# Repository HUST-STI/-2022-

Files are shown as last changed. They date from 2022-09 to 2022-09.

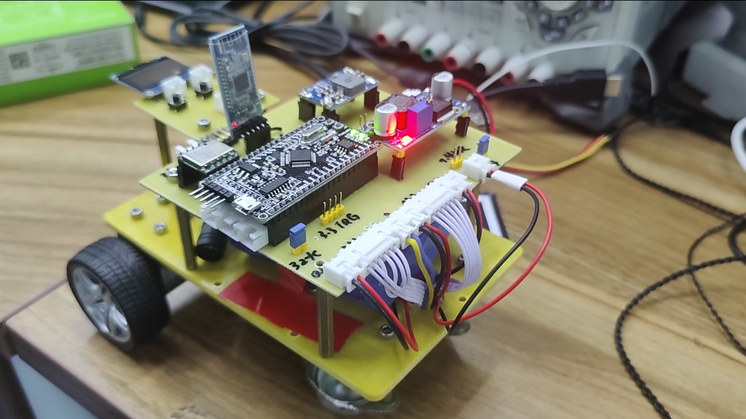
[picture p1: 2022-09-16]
小车图片.png

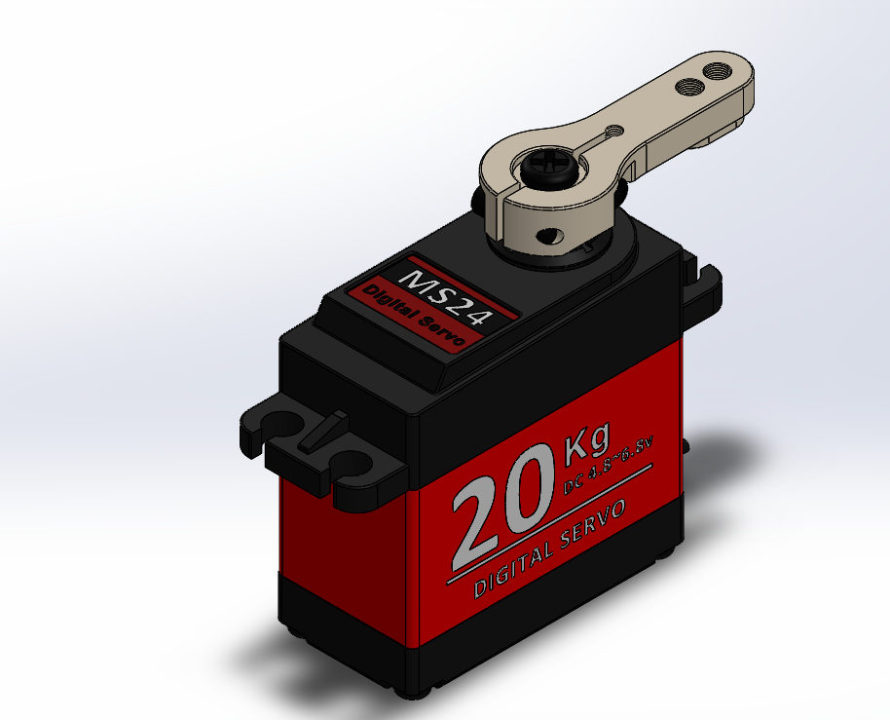
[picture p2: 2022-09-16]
机械结构/云台支架/000483伺服舵机外形模型3D图/三维总图.png

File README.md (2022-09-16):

# -2022暑期培训模拟题激光引导小车-
## 程序说明

由于是模拟题，所以就不详细介绍了，具体说说各部分怎么实现的就行

1. 小车云台通讯：两个BT-05蓝牙模块
2. 确保小车走直线：使用JY-901陀螺仪进行角度闭环，注意要设置该陀螺仪为六轴算法，这样角度才能用，九轴会飘
3. 确保小车走到指定格子：电机编码器速度环加位置环
4. 寻路算法：详见报告
5. 激光笔指到指定格子：定死云台位置，直接开环标定
6. 识别数字：Jetson Nano跑神经网络
7. 遥控选择数字：使用Arduino Uno连接红外接收头，收到信号后给STM32发信息即可。这样做是因为Arduino有现成的红外库，使用方便

## 机械说明

小车用的是牛眼轮差速转向结构，这种结构适合在小范围内灵活移动，为了确保不打滑，小车重心应该压在后轮上。

云台没什么好说的，就是直接用2020铝材支起来一个架子，在架子上放电路。舵机固定方式看文件内的Solidwork文件。

工程来自K06

2022.9.16

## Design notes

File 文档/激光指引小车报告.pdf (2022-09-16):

## 激光引导小车

摘要：本系统实现了一个激光发射云台和一辆激光引导的小车。云台利用 STM32 主控制

器完成舵机控制，驱动激光笔的运动，采用 Jetson Nano 作为图像处理单元，通过深度神经

网络完成数字和黑块的识别功能，选用BT-05蓝牙模块作为通信单元。小车系统利用STM32

主控制器和电机驱动模块完成电机控制，驱动小车运动，通过 BT-05 蓝牙模块与云台进行

通信。最终，云台可以实现识别数字和障碍块、使激光指向目标点、与小车通信等功能；

小车可以完成接收云台信号，移动到指定目标点并返回等任务。

关键词：神经网络；运动控制；PID 算法。

第1页

一、 系统方案

1. 比较与选择

1.1 机器视觉方案

方案一：OpenMV

方案二：Jetson Nano

方案比较与选择： 方案一使用 OpenMV 进行视觉处理。使用该模块进行图像处理十分简

单便捷，且不会存在自启动、开发环境配置等问题。但受处理器性能限制，OpenMV 的处

理速度慢、运行内存小，不适合复杂的图像处理。方案二采用 Jetson Nano 上运行 OpenCV

的方式进行图像处理。该方案优点是 Jetson Nano 搭载了 NVIDIA 显卡，处理速度块，运行

内存大，而且 OpenCV 内置函数功能齐全，完全满足复杂的图像处理需求。但缺点是与

STM32 通讯困难且开发流程繁琐。在本装置中，为增强系统对数字识别的准确度，需要使

用深度神经网络来提取图片特征并推理，运算复杂而且涉及到多帧图像处理，速度慢、内

存小的 OpenMV 已不能满足系统的需求。因此选择 Jetson Nano 进行图像识别。

1.2 小车底盘方案选择

方案一：阿克曼转向

方案二：后轮差速转向

方案比较与选择：方案一的优点在于控制算法比较简单，只需要控制前轮转角即可控制小

车的转向角度；缺点是小车的体积会比较大，小车转弯半径大，不适合大角度转弯、掉头

等操作。方案二的优点在于小车可以进行原地掉头等灵活的运动，小车体积小；缺点是小

车只能在比较平坦的地面上行进。在激光引导小车任务中，地形平坦，需要小车进行灵活

的运动。综合分析，选择两轮差速转向结构。

1.3 直行矫正方案选择

方案一：阿克曼转向

方案二：后轮差速转向

方案比较与选择：方案一的优点在于摄像头可以实时反映小车前进方向偏离路径中心线的

距离，实现小车绝对地直行；缺点在于算法复杂，并且需要额外的处理器和外围电路。方

案二的优点在于角度传感器的电路和算法并不复杂，模块体积小，功耗低，使用起来十分

方便；缺点为角度传感器的零点方向并不一定与行驶方向重合，有一定的偏差。在激光引

导小车任务中，小车的行驶路线并不复杂，任务对小车的行驶角度要求不高，综合分析，

选择角度传感器矫正方案。

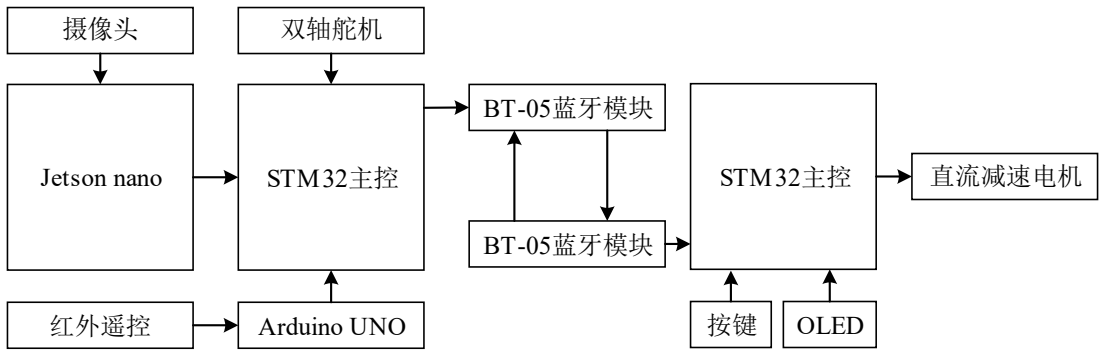
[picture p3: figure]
STM32主控; 直流 速电机; BT-05蓝牙模块; Jetson nano; 摄像头; 红外遥控; Arduino UNO

第2页

2. 方案描述

系统框图如图 1 所示。本系统通过 Arduino 主控的红外遥控系统控制激光笔指向区域和

小车运动的模式。系统使用 Jetson Nano 作为图像处理单元，通过图像处理的方式获得地图障

碍区域位置，并通过 UART 串口通讯将数据传输给 STM32 主控制器。主控制器接收到数据

后控制云台舵机姿态和小车的直流编码电机，将激光笔指向指定区域并控制小车避开障碍到

达目的区域。云台和小车之间通过 BT-05 蓝牙模块实现通讯。

图 1 系统框图

二、 理论分析与计算

1. 数字识别

数字识别部分采用深度神经网络模型 Yolov4-tiny。其结构图如图 2 所示。Yolov4-tiny

模型的参数量只有 600 万，在目标检测领域的深度神经网络中参数量较少，比较适合在嵌

入式设备上进行实时检测推理。其整体网络结构共有 38 层，使用了三个残差单元，激活函

数使用了 LeakyReLU,目标的分类与回归使用两个特征层，合并有效特征层时使用了特征

金字塔网络。其同样使用了 CSPnet 结构，并对特征提取网络进行通道分割，将经过 3x3 卷

积后输出的特征层通道划分为两部分，并取第二部分。相较于其它深度识别网络，Yolov4-

tiny 的实时性和准确率均有所提高。

在本装置中，使用现场拍摄的的照片作为原始数据集，一种拍摄了约 900 张图片，包

含 8 中数字。对原始数据集做 Mosaic 数据增强后得到月 4000 张数据集。将其划分为训练

集和测试集后送入模型中训练。最终得到的测试集精度达到了 90%以上，经实际测试，模

型的泛化误差较小，检测帧率能够达到 20 帧左右，符合设定的任务要求。

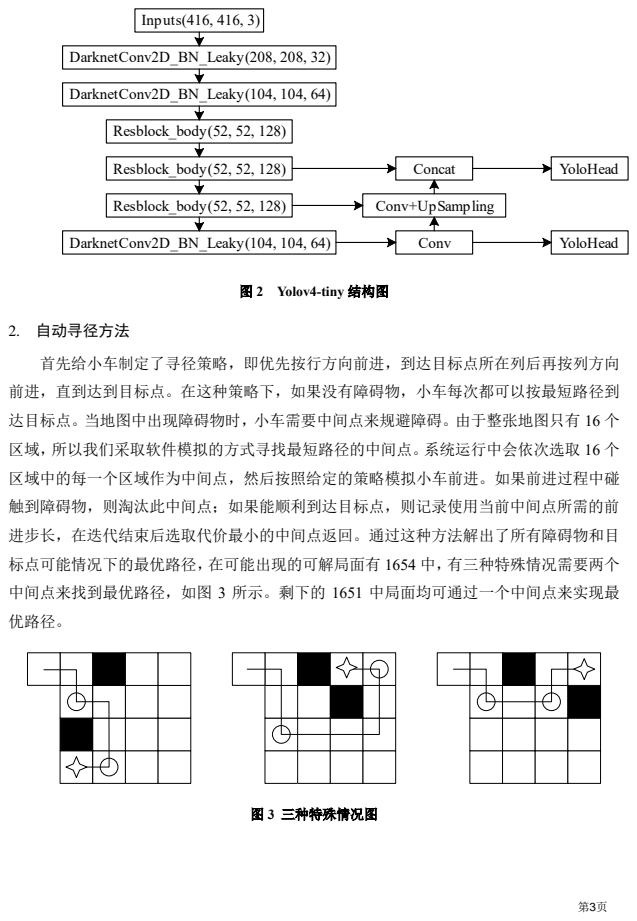
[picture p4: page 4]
图 2 Yolov4-tiny 结构图; 2. 自动寻径方法; 图 3 三种特殊情况图; Inputs 416, 416, 3; DarknetConv2D BN Leaky 208, 208, 32; DarknetConv2D BN Leaky 104, 104, 64; Concat; Yolo ead; Conv

Res lock ody 52, 52, 128

Conv UpSa plin

首先给小车制定了寻径策略，即优先 行方向前进，到达目标点所在列后再 列方向
前进，直到达到目标点。在这种策略下，如果没有障碍物，小车每次都可以 最短路径到
达目标点。当地图中出现障碍物时，小车需要中间点来规避障碍。由于整张地图只有 16 个
区域，所以我们采取软件模拟的方式寻找最短路径的中间点。系统运行中会依次选取 16 个
区域中的每一个区域作为中间点，然后 照给定的策略模拟小车前进。如果前进过程中碰
触到障碍物，则淘汰此中间点；如果能顺利到达目标点，则记录使用当前中间点所需的前
进步长，在迭代结束后选取代价最小的中间点返回。通过这种方法解出了所有障碍物和目
标点可能情况下的最优路径，在可能出现的可解局面有 1654 中，有三种特殊情况需要两个
中间点来找到最优路径，如图 3 所示。剩下的 1651 中局面均可通过一个中间点来实现最
优路径。

第4页

3. 两轮差速底盘结构

本小车的底盘采用两轮差速底盘结构，该结构通过两个橡胶车轮和两个牛眼轮对底盘

进行支撑，如图 4 所示。

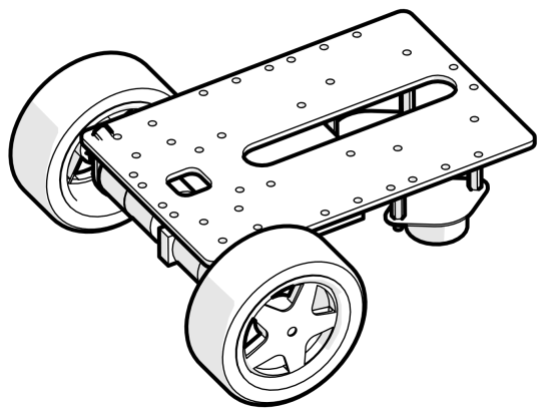
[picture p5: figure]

图 4 两轮差速底盘结构
设车体速度为 v，左轮速度为
l

v

，右轮速度为
r

v

，车体自转速度为
ω

，转弯半径为 R，

两轮之间距离为 D，两轮到车中心的距离为 d，右轮到圆心距离为 L。我们可以推算出整

车角速度和两轮速度之间的关系如下

角速度、速度和运动半径之间的物理关系：

| | v | R =ω*
3.1
左轮、右轮速度分解：
*( | ) | *( | 2 ) | *( | ) l
v | L D | L | d | R d | d = | + | = | + | = | + | = ω | ω | ω | ω
3.2
* | *( | ) r | l v | v | L | R d | v | d = | = | = | − | = − ω | ω | ω
3.3
和速度等于两轮速度之和的一半：
* | *( | )
2
l | r v | v v | R | L d ω | ω
+
= | = | + | =

3.4

角速度和两轮差速之间的关系如式 3.5 所示：

2

l | r v | v
d

ω

−
=

3.5

因此只要控制两个车轮的差速，小车就可以进行前进、后退、转向和原地掉头等操作。

4. 串级 PID 与直行矫正

我们采用 PID 算法对小车每个车轮的转动速度和转动角度进行控制。在小车从初始区

域出发到达指定区域过程中，只使用了速度环来控制小车的前行速度。

电机在转动时，单片机会对编码器输出的矩形波进行捕获，随后计算出电机的实时转

速反馈到输出到电机的 PWM 信号中，实现对速度的控制。

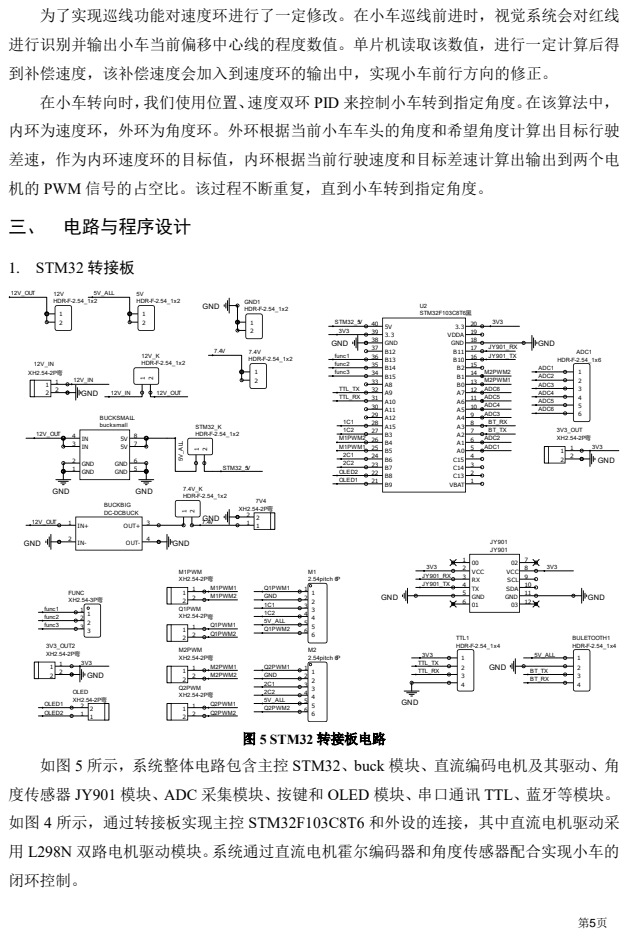
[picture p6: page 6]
三、 电路与程序设计; 1. STM32 转接板; 图 5 STM32 转接板电路; 路电机驱动模块。系统通过直流电机霍尔编码器和角度传感器配合实现小车的

为了实现巡线功能对速度环进行了一定修改。在小车巡线前进时，视觉系统会对红线
进行识别并输出小车当前偏移中心线的程度数值。单片机读取该数值，进行一定计算后得
到补偿速度，该补偿速度会加入到速度环的输出中，实现小车前行方向的修正。
在小车转向时，我们使用位置、速度 环 PID 来控制小车转到指定角度。在该算法中，
内环为速度环，外环为角度环。外环根据当前小车车头的角度和希望角度计算出目标行驶
差速，作为内环速度环的目标值，内环根据当前行驶速度和目标差速计算出输出到两个电
机的 PWM 信号的占空比。该过程不断重复，直到小车转到指定角度。

如图 5 所示，系统整体电路包含主控 STM32、 uck 模块、直流编码电机及其驱动、角
度传感器 JY901 模块、ADC 采集模块、 键和 OL D 模块、串口通讯 TTL、蓝牙等模块。
如图 4 所示，通过转接板实现主控 STM32F103C8T6 和外设的连接，其中直流电机驱动采
闭环控制。

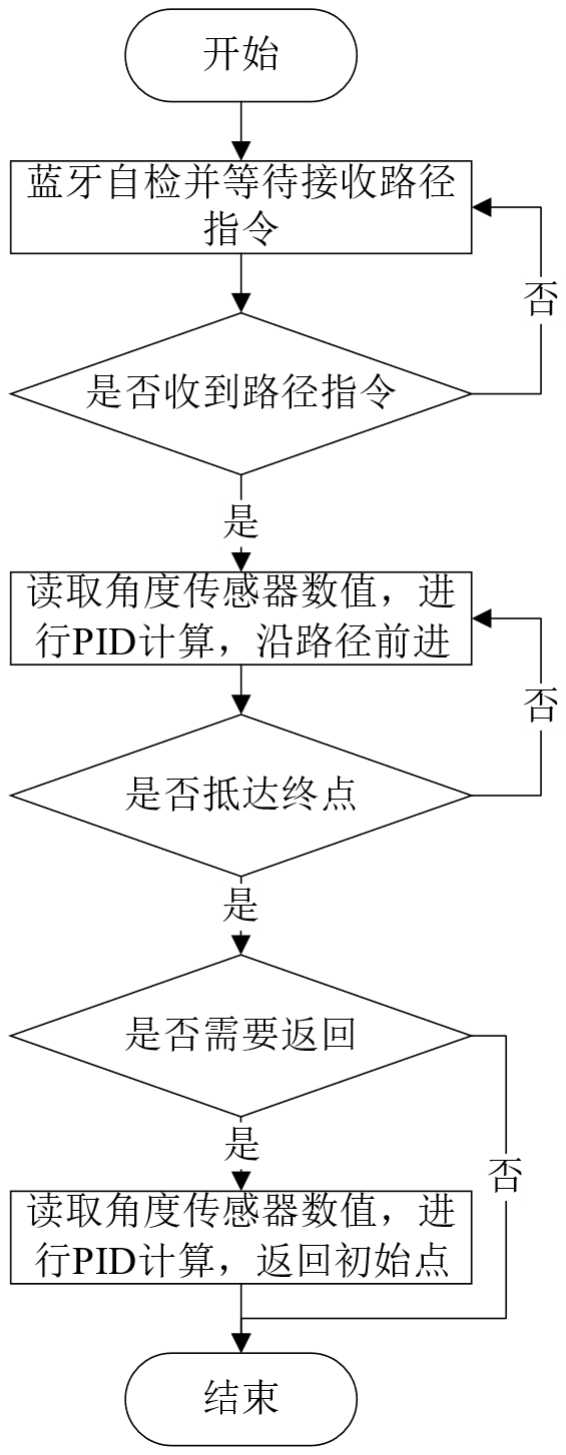
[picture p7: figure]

第6页

2. 软件程序设计

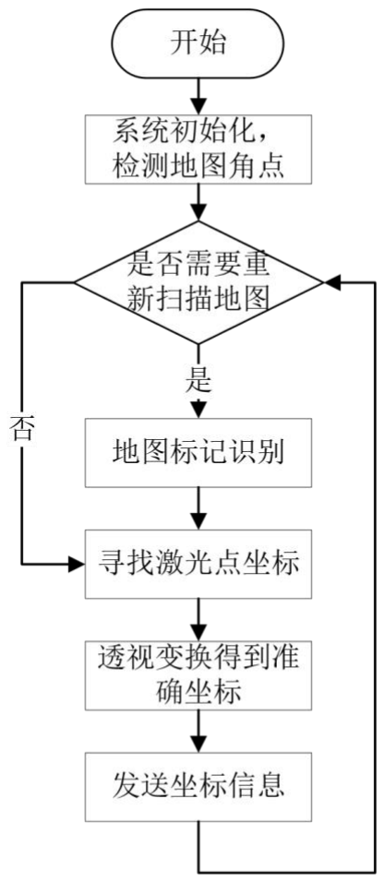
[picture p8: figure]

图 6 程序框图
小车在程序开始后，会先进入蓝牙传输自检阶段，只有收到来自云台的指令，程序才 会进入路径接收阶段。在路径接收阶段中，小车会等待接收云台发送的路径，路径包括 一个中间点和目标点。小车会 照一定的路线先行驶到中间点，随后再行驶到终点。如 果需要返回停车坪，小车会在停止 2 秒后原路返回。

四、 测试方案与测试结果

测试环境

类型 | 品牌 | 型号
电源 | Zhon Ce | DF1743003C 型稳压源
其他 | 卡西欧 | S-70W 型秒表

第7页

1. 测试方案

1.1 基本要求

控制激光笔指向 0、1、4、5 区域，摄像头识别激光点并控制小车移动到指定区域，停

留超过 2s，记录激光笔指向区域编号和总运动时间；在此基础上新增 2、6、8、9、A 区域，

重复上述操作；在此基础上控制激光笔指向任何一个区域，重复上述操作。

1.2 发挥部分

选取场地中的 1 个区域为障碍区域，并使用黑色色块覆盖，控制激光笔指向非障碍区

域，摄像头识别激光点并控制小车绕过障碍区域移动到指定区域，停留超过 2s，记录激光

笔指向区域编号、障碍区域编号和总运动时间；在此基础上选取场地中的 2 个区域为障碍

区域，重复上述操作；在此基础上不重复交换任意两组区域，重复上述操作。

2. 测试结果与数据

2.1 基本要求
表 1 基础部分测试
序号 | 指向区域编号 | 总运动时间/s
1 | 4 | 5.4
2 | 6 | 11.5
3 | B | 15.3
4 | F | 17.9

2.2 发挥部分
表 2 发挥部分：两个小车协同送药测试
序号 | 指向区域编号 | 障碍区域编号 | 总运动时间/s
1 | 6 | 2 | 13.3
2 | A | 6 | 15.9
3 | 7 | 3、6 | 23.3
4 | C | 8、9 | 27.4

第8页

3. 测试结果分析

3.1 基础要求

由测试结果知，系统控制激光笔指向任何区域，摄像头识别激光点并控制小车移动到

指定区域停留超过 2s，均满足题目要求。

3.2 发挥部分

由测试结果知，选取 1 个或者 2 个区域为障碍区域，系统控制激光笔指向非障碍区域，

摄像头识别激光点并控制小车绕过障碍区域移动到指定区域，满足题目要求。在测试过程

途中车身投影未接触障碍区域，很好的完成了题目的要求。

综上所述，本系统能够完成题目的基本要求和发挥要求。

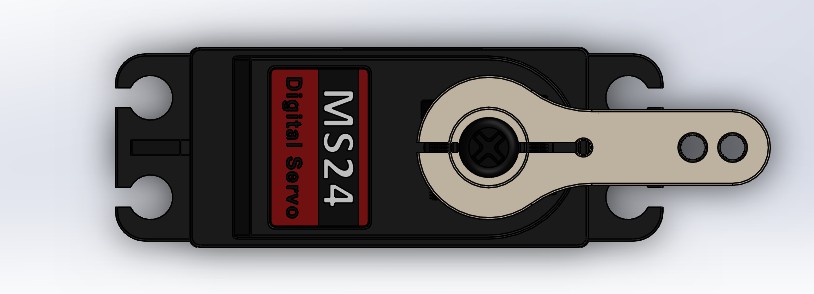
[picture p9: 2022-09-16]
机械结构/云台支架/000483伺服舵机外形模型3D图/俯视图.png

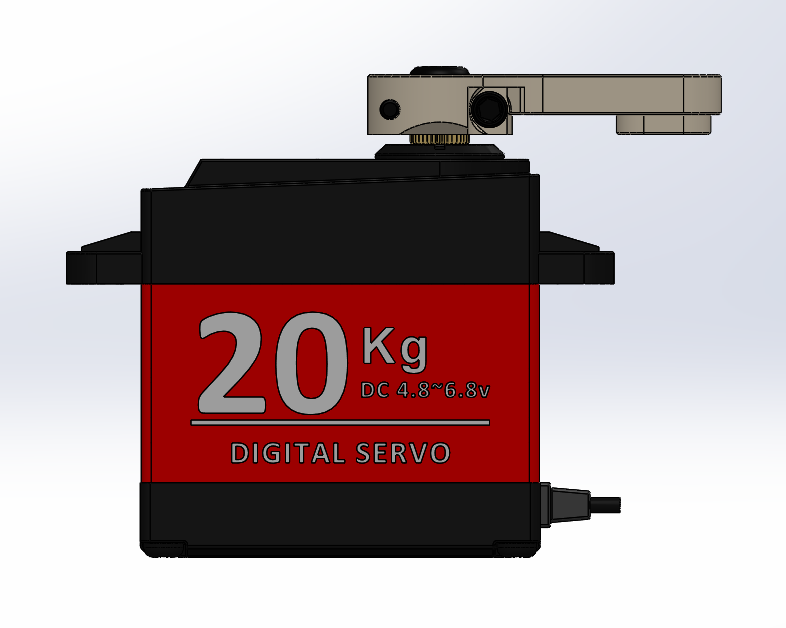
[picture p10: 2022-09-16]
机械结构/云台支架/000483伺服舵机外形模型3D图/主视图.png

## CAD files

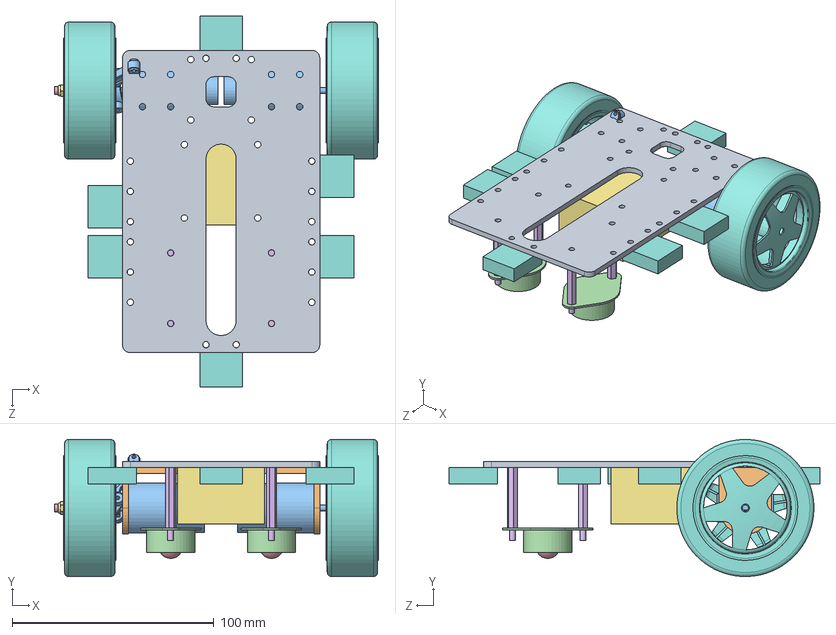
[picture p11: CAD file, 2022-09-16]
机械结构/车/激光引导小车装配体.SLDASM
160.9 x 68.0 x 184.0 mm
车底板
JGA25-370直流减速电机支架 x 2
MG310电机（霍尔编码器） x 2
CY-12A万向球 x 2
CY-12A万向球的球 x 2
铜柱 高20M3螺纹 x 4
L298N简化
l轮子T x 2
灰度传感器 x 6

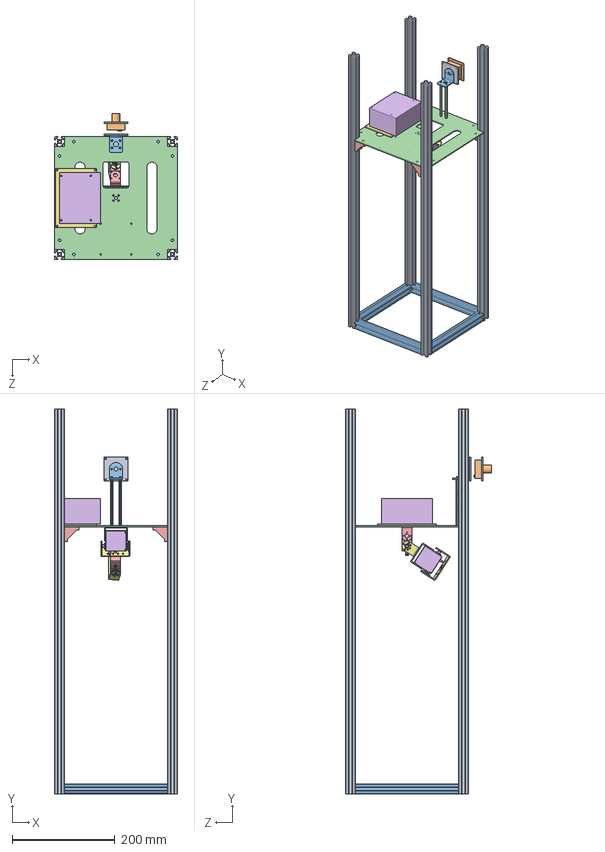
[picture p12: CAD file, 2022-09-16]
机械结构/云台支架/摄像头支架.SLDASM
239.8 x 750.0 x 284.8 mm
竖直支撑钢管 x 4
1车摄像头
摄像头支架横着 x 4
云台支撑板
RDS3115短U支架 x 2
RDS3115 x 2
RDS3115长U支架 x 2
舵机副转盘 x 2
1车摄像头转接2
1车摄像头转接
JGA25-370直流减速电机支架
铜柱 高20M3螺纹 x 6
钢管转角小三角 x 4

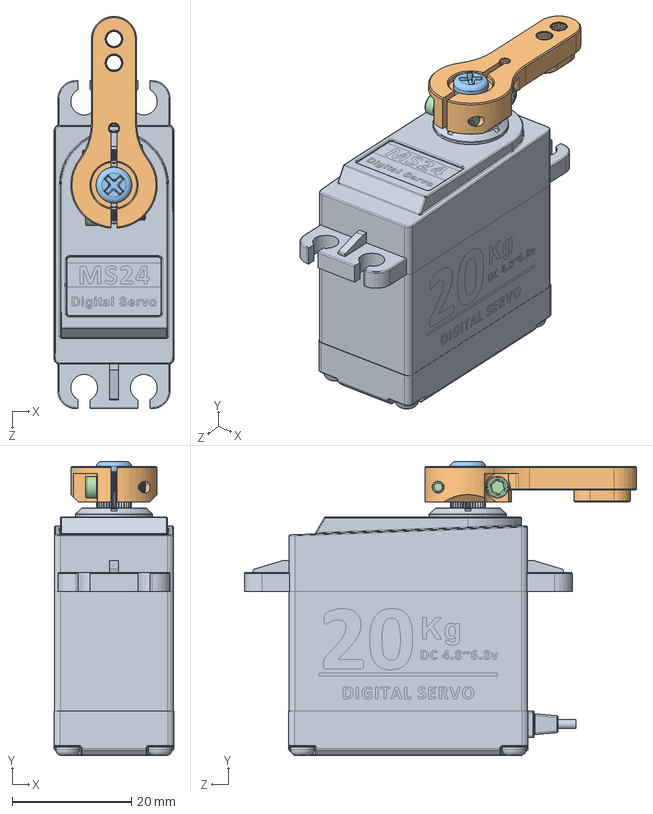
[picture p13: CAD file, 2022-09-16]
机械结构/云台支架/000483伺服舵机外形模型3D图/DIGITAL SERVO ASSEMBLY.SLDASM
20.1 x 49.3 x 65.8 mm
DS3218MG MS24 Digital Servo 270
Servo Arm for DS3218MG
Screw-01 for DS3218MG
Screw-02 for DS3218MG x 2

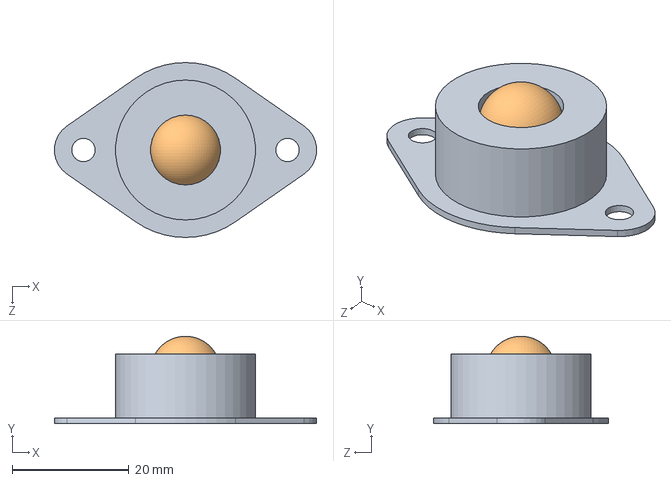
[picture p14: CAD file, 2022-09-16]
机械结构/车/CY-12A万向球组合体.SLDASM
44.9 x 15.0 x 30.0 mm
CY-12A万向球
CY-12A万向球的球

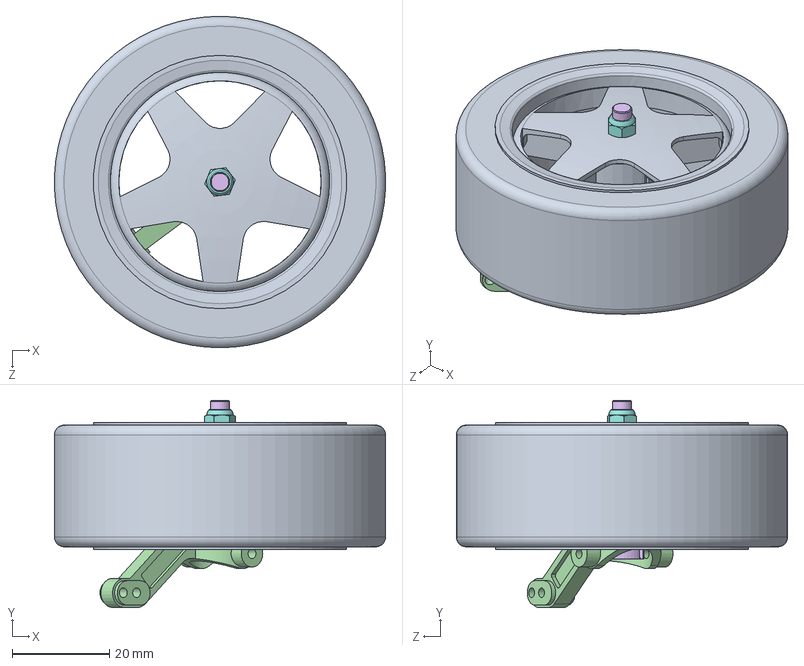
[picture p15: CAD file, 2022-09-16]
机械结构/车/转向结构新/轮子套件.SLDASM
67.9 x 42.5 x 68.0 mm
l轮子T
0388轴承
0288轴承
转向杯
六角轮座
金属轮座轴 新
圆销
GB6170-M4自锁-ZN-10

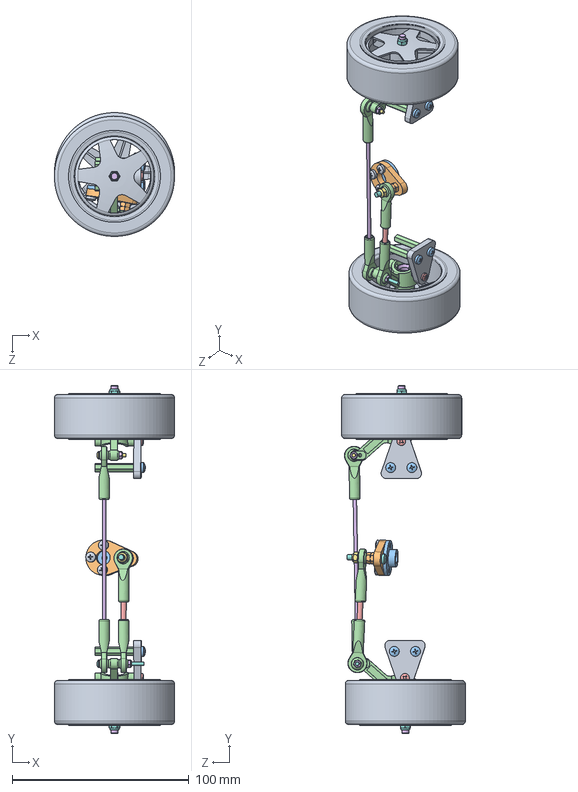
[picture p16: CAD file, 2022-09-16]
机械结构/车/转向结构新/转向套件.SLDASM
68.0 x 196.9 x 70.1 mm
l轮子T x 2
0388轴承 x 2
0288轴承 x 2
转向杯 x 2
六角轮座 x 2
金属轮座轴 新 x 2
圆销 x 2
GB6170-M4自锁-ZN-10 x 2
板1 x 2
板2
金属舵盘
球头轴承 x 4
螺杆m3x25
螺杆m3x75
GB6170-M3（自锁）
GB818-M3X20-ZN-4.8
GB818-M3X6-ZN-4.8 x 3
GB6170-M3-ZN-10 x 2
GB818-M3X8-ZN-4.8 x 4
M3X20双通铜柱 - 副本 x 4
GB845-ST38 x 2
GB6170-M2（自锁） x 2
GB818-M2X15
GB818-M2X25

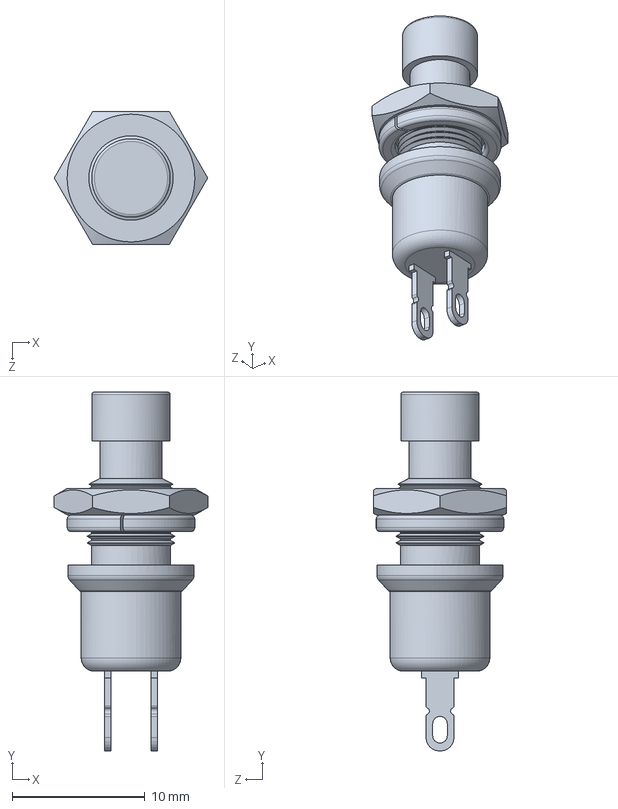
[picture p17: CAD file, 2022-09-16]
机械结构/云台支架/000483伺服舵机外形模型3D图/Momentary Switch Red Cap.SLDPRT
11.5 x 27.0 x 10.0 mm

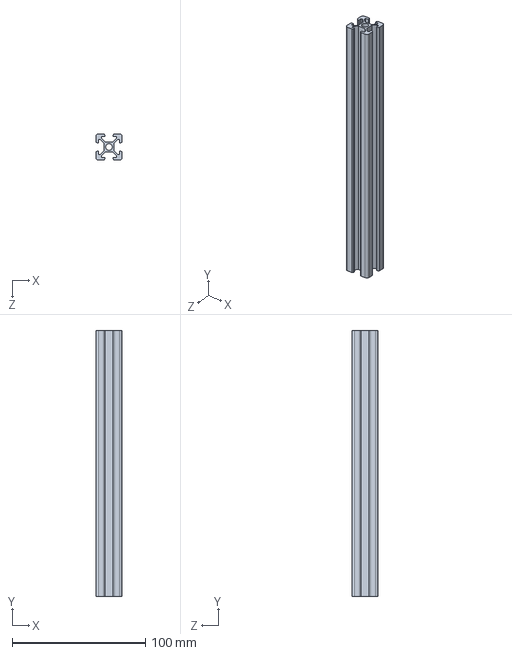
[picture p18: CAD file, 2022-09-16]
机械结构/云台支架/摄像头支架横着.SLDPRT
19.9 x 200.0 x 19.9 mm

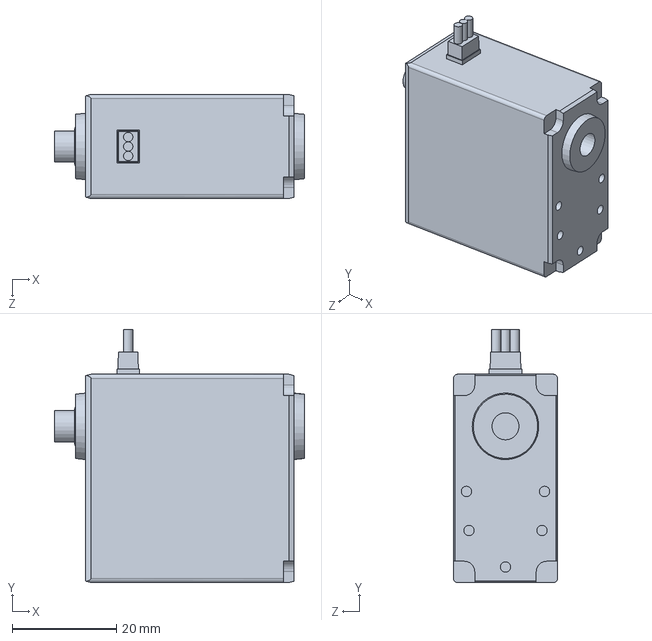
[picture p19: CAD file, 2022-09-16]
机械结构/云台支架/舵机RDS3115MG/RDS3115.SLDPRT
48.0 x 48.6 x 20.0 mm

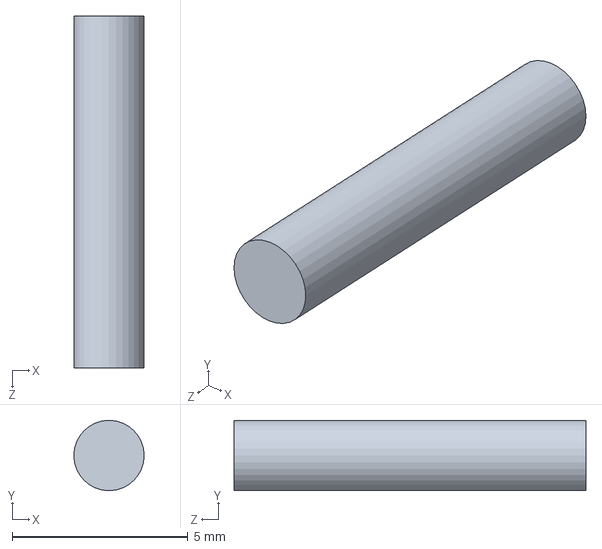
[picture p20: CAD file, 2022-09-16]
机械结构/车/转向结构新/圆销.SLDPRT
2.00 x 2.00 x 10.0 mm

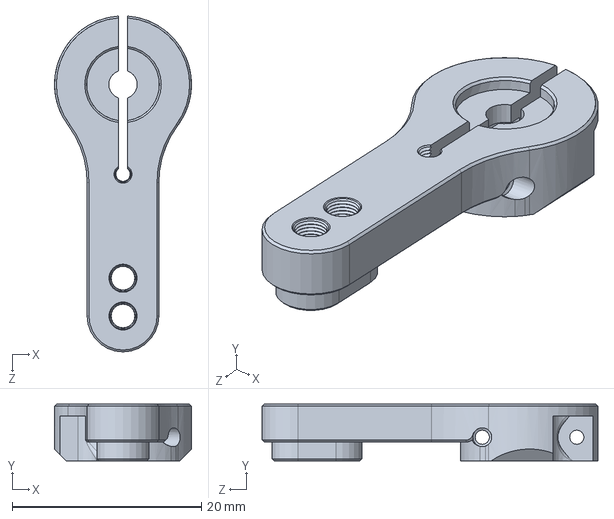
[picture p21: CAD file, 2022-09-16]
机械结构/云台支架/000483伺服舵机外形模型3D图/Servo Arm for DS3218MG.SLDPRT
14.5 x 6.00 x 35.5 mm

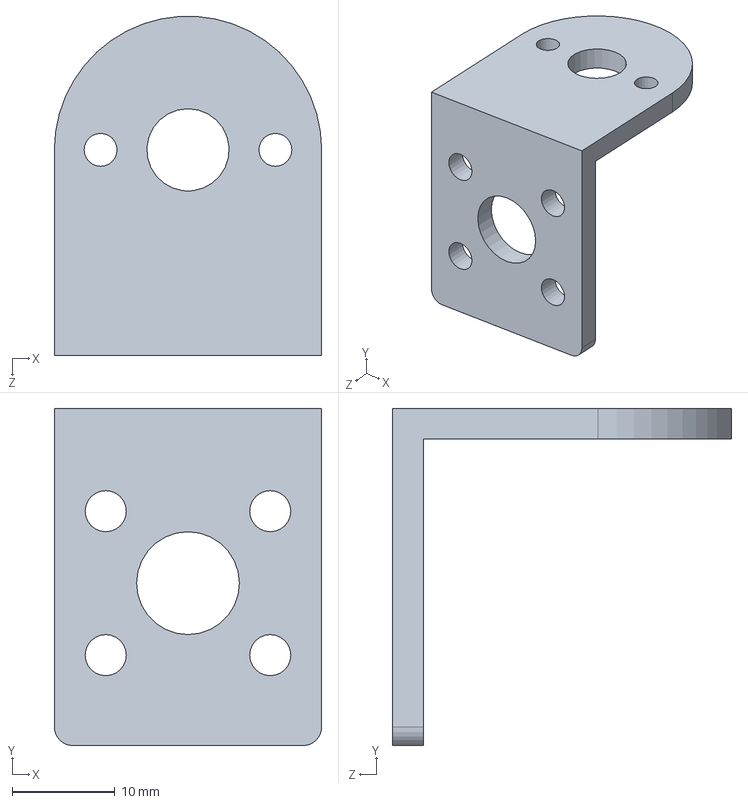
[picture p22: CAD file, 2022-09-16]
机械结构/云台支架/JGA25-370直流减速电机支架.SLDPRT
26.0 x 32.8 x 33.0 mm

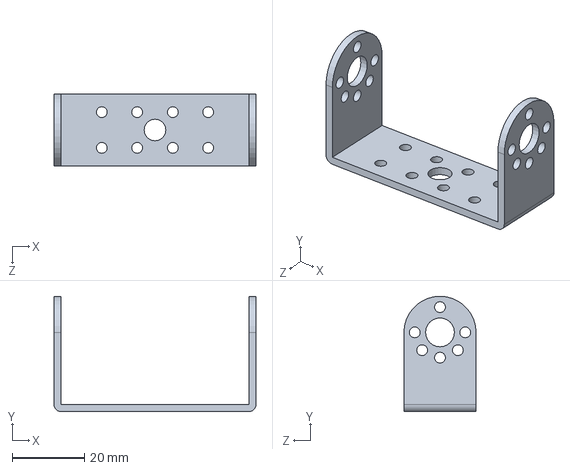
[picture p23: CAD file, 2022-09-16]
机械结构/云台支架/舵机RDS3115MG/RDS3115长U支架.SLDPRT
56.0 x 32.0 x 20.0 mm

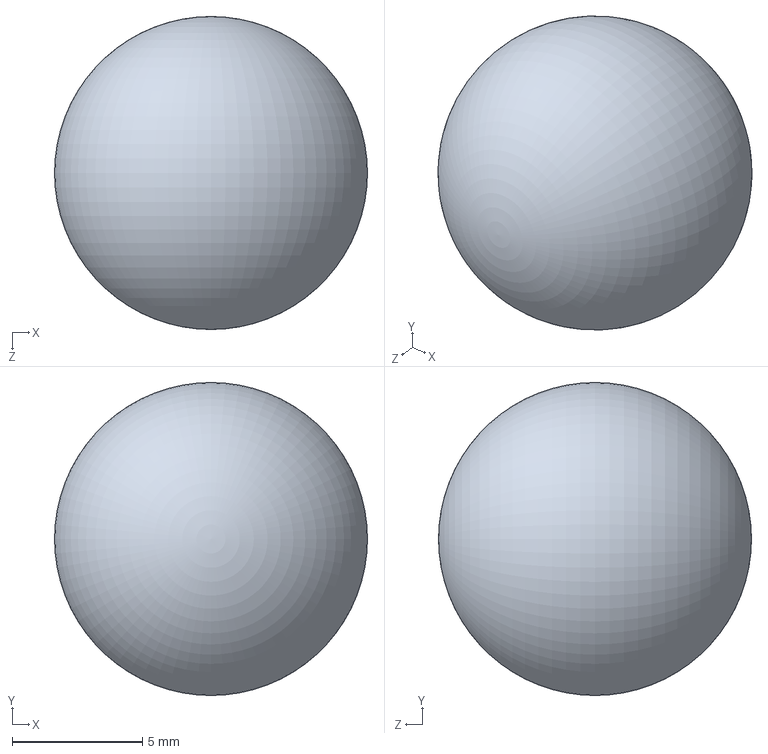
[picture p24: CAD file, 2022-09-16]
机械结构/车/CY-12A万向球的球.SLDPRT
12.0 x 12.0 x 12.0 mm

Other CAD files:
机械结构/云台支架/舵机RDS3115MG/RDS3115MG双轴数码舵机.SLDASM
机械结构/车/转向结构新/GB818-M2X25.SLDPRT
机械结构/云台支架/000483伺服舵机外形模型3D图/DS3218MG MS24 Digital Servo 270.SLDPRT
机械结构/云台支架/jetson nano 简化.SLDPRT
机械结构/云台支架/000483伺服舵机外形模型3D图/Screw-01 for DS3218MG.SLDPRT
机械结构/云台支架/000483伺服舵机外形模型3D图/Screw-02 for DS3218MG.SLDPRT
机械结构/云台支架/1车摄像头.SLDPRT
机械结构/云台支架/1车摄像头转接.SLDPRT
机械结构/云台支架/1车摄像头转接2.SLDPRT
机械结构/云台支架/jetson nano转接板.DXF
机械结构/云台支架/jetson nano转接板.SLDPRT
机械结构/云台支架/云台支撑板.DXF
机械结构/云台支架/云台支撑板.SLDPRT
机械结构/云台支架/激光笔转接板.DXF
机械结构/云台支架/激光笔转接板.SLDPRT
机械结构/云台支架/竖直支撑钢管.SLDPRT
机械结构/云台支架/舵机RDS3115MG/RDS3115短U支架.SLDPRT
机械结构/云台支架/舵机RDS3115MG/舵机主转盘.SLDPRT
机械结构/云台支架/舵机RDS3115MG/舵机副转盘.SLDPRT
机械结构/云台支架/舵机RDS3115MG/转轴.SLDPRT
机械结构/云台支架/钢管转角小三角.SLDPRT
机械结构/云台支架/铜柱 高20M3螺纹.SLDPRT
机械结构/车/CY-12A万向球.SLDPRT
机械结构/车/JGA25-370直流减速电机支架.SLDPRT
机械结构/车/L298N简化.SLDPRT
机械结构/车/MG310电机（霍尔编码器）.SLDPRT
机械结构/车/灰度传感器.SLDPRT
机械结构/车/车底板.DXF
机械结构/车/车底板.SLDPRT
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

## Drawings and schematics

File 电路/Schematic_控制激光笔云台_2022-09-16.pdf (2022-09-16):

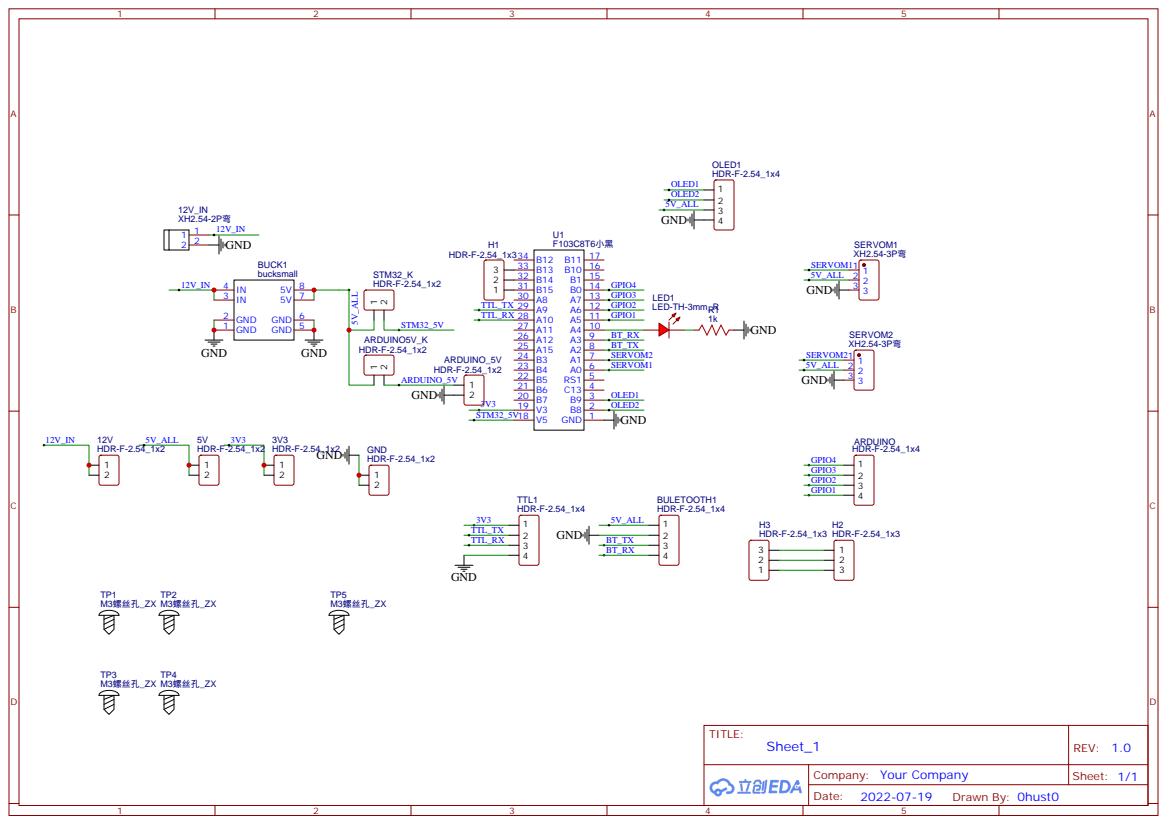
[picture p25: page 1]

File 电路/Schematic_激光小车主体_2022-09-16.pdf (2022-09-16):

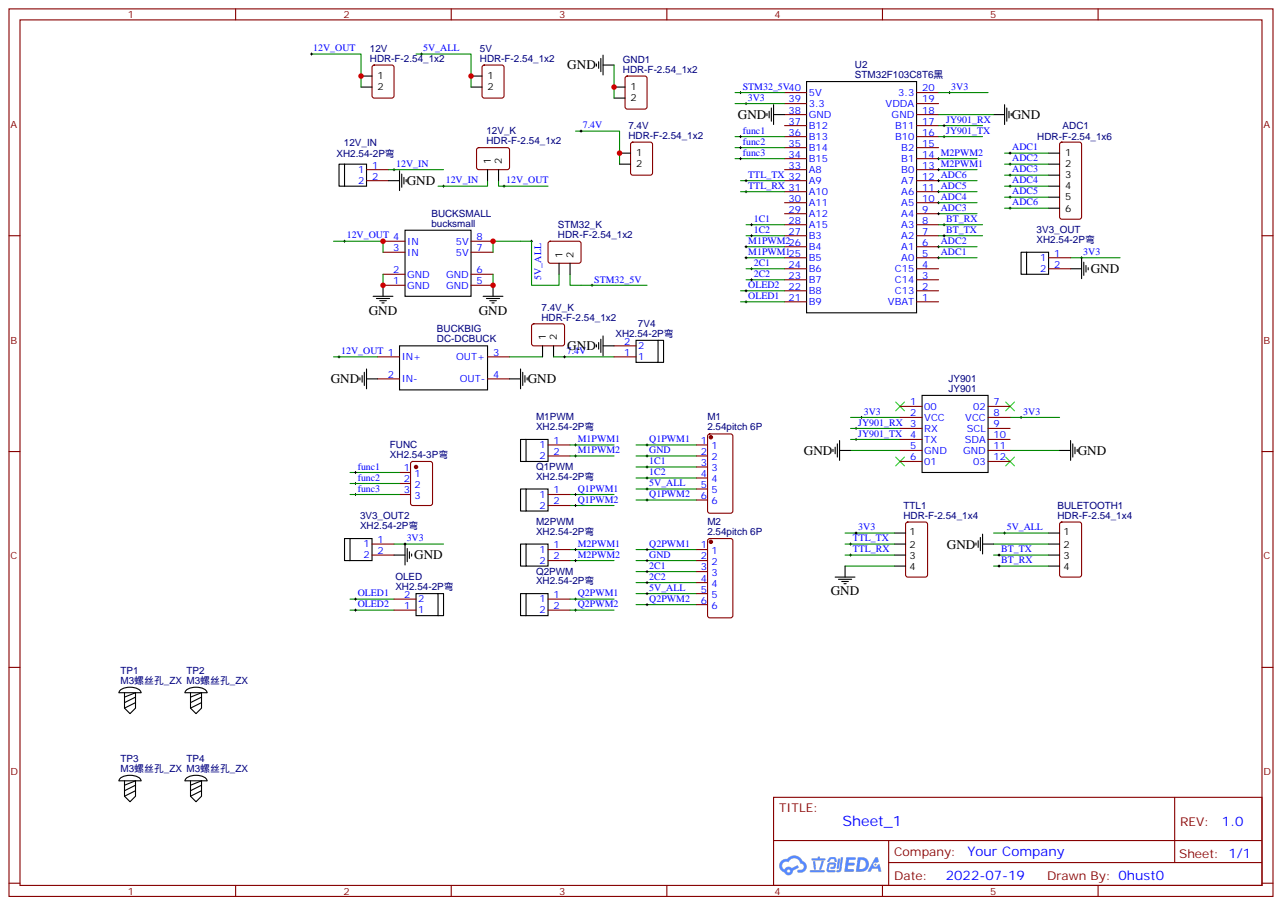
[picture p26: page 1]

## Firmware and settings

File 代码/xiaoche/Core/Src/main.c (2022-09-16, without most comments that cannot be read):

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
/* Includes ------------------------------------------------------------------*/
#include "main.h"
#include "adc.h"
#include "dma.h"
#include "tim.h"
#include "usart.h"
#include "gpio.h"

/* USER CODE BEGIN Includes */
#include <stdio.h>
#include "bluetooth.h"
#include "oled.h"
#include "g_sensor.h"
#include "encoder.h" 
#include "PID.h"
#include "control.h"
#include "JY901.h"
#include "button.h"
/* USER CODE END Includes */

/* USER CODE BEGIN PTD */
void Car_All_Init(void);

/* USER CODE END PTD */

/* USER CODE BEGIN PM */
extern float angle_z,angle_z_last,angle_z_all;
extern int32_t angle_z_temp;
extern uint8_t init_count;
extern int32_t JY901_Init_val[4];
extern int8_t jy901_of_count;
uint8_t run_mode = 0,run_mode_temp = 1;
extern int32_t tar_angle;
extern  uint8_t speed_flag,angle_flag;
int32_t tar_direct = 0;
extern uint8_t get_mode;
extern uint8_t tar_point[4];
/* USER CODE END PM */


void SystemClock_Config(void);
/* USER CODE BEGIN 0 */
/*********************************
* ��������DMA_Usart_Send
* ����˵�������ڷ��͹��ܺ���
*	�βΣ�buf, len
*	����ֵ����
*********************************
*/
void DMA_Usart_Send(uint8_t*buf, uint8_t len)
{
	if(HAL_UART_Transmit_DMA(&huart3, buf, len) != HAL_OK)
	{
		//printf("error tansmit");

		//Error_Handler();
	}
}
/*
*********************************
* ��������DMA_Usart_Read
* ����˵�������ڽ��չ��ܺ���
*	�βΣ�data, len
*	����ֵ����
*********************************
*/
void DMA_Usart_Read(uint8_t* data, uint8_t len)
{
	HAL_UART_Receive_DMA(&huart3, data, len);
}
/* USER CODE END 0 */

/**
  * @brief  The application entry point.
  * @retval int
  */
int main(void)
{
  /* MCU Configuration--------------------------------------------------------*/

  /* Reset of all peripherals, Initializes the Flash interface and the Systick. */
  HAL_Init();

  /* Configure the system clock */
  SystemClock_Config();

  /* Initialize all configured peripherals */
  MX_GPIO_Init();
  MX_USART1_UART_Init();
  MX_ADC1_Init();
  MX_TIM1_Init();
  MX_TIM2_Init();
  MX_TIM3_Init();
  MX_TIM4_Init();
  MX_DMA_Init();
  MX_USART3_UART_Init();
  MX_USART2_UART_Init();
  /* USER CODE BEGIN 2 */
  Car_All_Init();
  printf("start\r\n");
  __HAL_UART_ENABLE_IT(&huart3, UART_IT_IDLE);  
	HAL_UART_Receive_DMA(&huart3, rx_buffer, BUFFER_SIZE);

  OLED_ShowString(0,0,(unsigned char *)"blue checking",16);
  OLED_Refresh();
  Bluetooth_Self_Check();
  OLED_Clear();
  /* USER CODE END 2 */

  /* Infinite loop */
  /* USER CODE BEGIN WHILE */
  while (1)
  {
    /* USER CODE END WHILE */

    // /* USER CODE BEGIN 3 */
    if(run_mode == 0)
    {
      HAL_GPIO_WritePin(LIFE_LED_GPIO_PORT,LIFE_LED_GPIO_PIN,GPIO_PIN_RESET);//输出低
      if(get_mode == 2)
      {
        tar_direct = angle_z_all;
        run_mode = 2;
      }        
      else if(get_mode == 3)
      {
        tar_direct = angle_z_all;
        run_mode = 3;
      }
      else if(get_mode == 4)
      {
        tar_direct = angle_z_all;
        run_mode = 4;
      }
      else if(get_mode == 5)
      {
        tar_direct = angle_z_all;
        run_mode = 5;
      }
      else if(get_mode == 6)
      {
        tar_direct = angle_z_all;
        run_mode = 6;
      }
      else if(get_mode == 7)
      {
        tar_direct = angle_z_all;
        run_mode = 7;
      }
      OLED_ShowString(0,0,(unsigned char *)"choosing",16);
      OLED_Refresh();
    }
    if(run_mode != 0)
    {
      HAL_GPIO_WritePin(LIFE_LED_GPIO_PORT,LIFE_LED_GPIO_PIN,GPIO_PIN_SET);//输出低
      OLED_ShowString(0,0,(unsigned char *)"running",16);
      OLED_ShowString(0,16,(unsigned char *)"mode",16);
      OLED_ShowNum(0,32,run_mode,1,16);
      OLED_Refresh();
      get_mode = 0;
    }
    switch(run_mode)
    {
      case 0:
        break;
      case 2://一个点
        run_one(tar_point[0],tar_point[1]);
        break;
      case 3://一个点且返回
        run_three(tar_point[0],tar_point[1]);
        break;
      case 4://两个点
        run_four(tar_point[0],tar_point[1],tar_point[2],tar_point[3]);
        break;
      case 5:
        run_five();
        break;
      case 6:
        run_six();
        break;
      case 7:
        run_seven();
        break;   
      default:
        break;  
    }


    
    if(recv_end_flag == 1)  
		{
      if(rx_buffer[0] == 85 && rx_buffer[1] == 83)
      {
        angle_z = (float)((rx_buffer[7]<<8)|rx_buffer[6])/32768.0*180.0;
      }
      if(init_count<3 && angle_z_temp != 0)
      {
          JY901_Init_val[init_count++] = angle_z_temp;
      }
      else if(init_count == 3)
      {
          JY901_Init_val[init_count++] = (JY901_Init_val[0]+JY901_Init_val[1]+JY901_Init_val[2])/3;
      }
      if(angle_z > 300 && angle_z_last < 50) jy901_of_count--;
      else if(angle_z < 50 && angle_z_last > 300) jy901_of_count++;
      angle_z_all = angle_z + jy901_of_count * 360;
      angle_z_last = angle_z;//保存上一次的值
      angle_z_temp = angle_z_all;
			memset(rx_buffer, 0, rx_len);
    	rx_len = 0;
			recv_end_flag = 0;
			HAL_Delay(1);
			HAL_UART_Receive_DMA(&huart3, rx_buffer, BUFFER_SIZE);
		}
  }
    
  /* USER CODE END 3 */
}

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
/* USER CODE BEGIN 4 */
/******************************
 * 功能：进行各模块的初始化
 * 输入：无
 * 返回：无
 * ******************************/
void Car_All_Init(void)
{
  Motor_Init();//电机相关结构体与定时器初始化
  PID_Init();
  Bluetooth_Init();
  OLED_Init_Run();

}

/* USER CODE END 4 */
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


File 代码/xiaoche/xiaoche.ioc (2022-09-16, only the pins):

Mcu.UserName=STM32F103C8Tx
PA0-WKUP.Signal=ADCx_IN0
PA1.Signal=ADCx_IN1
PA10.Signal=USART1_RX
PA13.Signal=SYS_JTMS-SWDIO
PA14.Signal=SYS_JTCK-SWCLK
PA15.Signal=S_TIM2_CH1_ETR
PA2.Signal=USART2_TX
PA3.Signal=USART2_RX
PA4.Signal=ADCx_IN4
PA5.Signal=ADCx_IN5
PA6.Signal=ADCx_IN6
PA7.Signal=ADCx_IN7
PA9.Signal=USART1_TX
PB0.Signal=S_TIM3_CH3
PB1.Signal=S_TIM3_CH4
PB10.Signal=USART3_TX
PB11.Signal=USART3_RX
PB12.Signal=GPIO_Output
PB13.Signal=GPIO_Input
PB14.Signal=GPIO_Input
PB15.Signal=GPIO_Input
PB3.Signal=S_TIM2_CH2
PB4.Signal=S_TIM3_CH1
PB5.Signal=S_TIM3_CH2
PB6.Signal=S_TIM4_CH1
PB7.Signal=S_TIM4_CH2
PB8.Signal=GPIO_Output
PB9.Signal=GPIO_Output
PC13-TAMPER-RTC.Signal=GPIO_Output
PD0-OSC_IN.Signal=RCC_OSC_IN
PD1-OSC_OUT.Signal=RCC_OSC_OUT

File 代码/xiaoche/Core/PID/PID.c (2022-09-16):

#include "pid.h"
PID pid_l_speed,pid_l_position,pid_r_speed,pid_r_position;
extern Motor motor_right,motor_left;
extern float angle_z,angle_z_last,angle_z_all;
extern int16_t JY901_Init_val[4];

/**********************************
 * 功能：PID结构体参数初始化
 * 输入：无
 * 返回：无
 * *******************************/
void PID_Init(void)//PID参数初始化
{
    pid_l_speed.err = 0;
    pid_l_speed.integral = 0;
    pid_l_speed.maxIntegral = 1000;
    pid_l_speed.maxOutput = __HAL_TIM_GetAutoreload(&PWM_TIM);
    pid_l_speed.lastErr = 0;
    pid_l_speed.output = 0;
    pid_l_speed.kp = KP_l_speed;
    pid_l_speed.ki = KI_l_speed;
    pid_l_speed.kd = KD_l_speed;

    pid_r_speed.err = 0;
    pid_r_speed.integral = 0;
    pid_r_speed.maxIntegral = 1000;
    pid_r_speed.maxOutput = __HAL_TIM_GetAutoreload(&PWM_TIM);
    pid_r_speed.lastErr = 0;
    pid_r_speed.output = 0;
    pid_r_speed.kp = KP_r_speed;
    pid_r_speed.ki = KI_r_speed;
    pid_r_speed.kd = KD_r_speed;

    pid_l_position.err = 0;
    pid_l_position.integral = 0;
    pid_l_position.maxIntegral = 80;
    pid_l_position.maxOutput = __HAL_TIM_GetAutoreload(&PWM_TIM);
    pid_l_position.lastErr = 0;
    pid_l_position.output = 0;
    pid_l_position.kp = KP_l_position;
    pid_l_position.ki = KI_l_position;
    pid_l_position.kd = KD_l_position;

    pid_r_position.err = 0;
    pid_r_position.integral = 0;
    pid_r_position.maxIntegral = 80;
    pid_r_position.maxOutput = __HAL_TIM_GetAutoreload(&PWM_TIM);
    pid_r_position.lastErr = 0;
    pid_r_position.output = 0;
    pid_r_position.kp = KP_r_position;
    pid_r_position.ki = KI_r_position;
    pid_r_position.kd = KD_r_position;
}

/****************************************
 * 作用：速度环PID计算
 * 参数：PID参数结构体地址；目标值；反馈值
 * 返回值：无
 * ****************************************/
float Speed_PID_Realize(PID* pid,float target,float feedback)//一次PID计算
{
    // if(pid->err < 1 && pid->err > -1) pid->err = 0;//pid死区
    pid->err = target - feedback;
    pid->integral += pid->err;

    if(pid->ki * pid->integral < -pid->maxIntegral) pid->integral = -pid->maxIntegral / pid->ki;//积分限幅
    else if(pid->ki * pid->integral > pid->maxIntegral) pid->integral = pid->maxIntegral / pid->ki;

    //if(abs(pid->err - pid->lastErr) > 100) pid->integral = 0;

    pid->output = (pid->kp * pid->err) + (pid->ki * pid->integral) + (pid->kd * (pid->err - pid->lastErr));//全量式PID

    //输出限幅
    if(target >= 0)//正转时
    {
        if(pid->output < 0) pid->output = 0;
        else if(pid->output > pid->maxOutput) pid->output = pid->maxOutput;
    }
    else if(target < 0)//反转时
    {
        if(pid->output < -pid->maxOutput) pid->output = -pid->maxOutput;
        else if(pid->output > 0) pid->output = 0;
    }

    pid->lastErr = pid->err;

    return pid->output;
}

/****************************************
 * 作用：位置环PID计算
 * 参数：PID参数结构体地址；目标值；反馈值
 * 返回值：无
 * ****************************************/
float Location_PID_Realize(PID* pid,float target,float feedback)//一次PID计算
{
     if(pid->err < 3 && pid->err > -3) pid->err = 0;//pid死区
    pid->err = target - feedback;
    pid->integral += pid->err;

    if(pid->ki * pid->integral < -pid->maxIntegral) pid->integral = -pid->maxIntegral / pid->ki;//积分限幅
    else if(pid->ki * pid->integral > pid->maxIntegral) pid->integral = pid->maxIntegral / pid->ki;

    pid->output = (pid->kp * pid->err) + (pid->ki * pid->integral) + (pid->kd * (pid->err - pid->lastErr));//全量式PID

    //输出限幅
    if(pid->output > pid->maxOutput) pid->output = pid->maxOutput;
    if(pid->output < -pid->maxOutput) pid->output = -pid->maxOutput;

    pid->lastErr = pid->err;

    return pid->output;
}

/****************************************
 * 作用：设置左边电机速度
 * 参数：PID参数结构体地址；目标值；反馈值
 * 返回值：无
 * ****************************************/
void Set_Left_Speed(float target,int16_t ad_speed)
{
    float pid_out = 0;
    if(target >= 180) target = 180;
    if(target < -180) target = -180;
    target = target + ad_speed;
    pid_out = Speed_PID_Realize(&pid_l_speed,target,motor_left.speed);
    //printf("pid_out = %.1f\r\n",pid_out);
    //printf("ad_speed = %d\r\n",ad_speed);
    //printf("pid_i = %.2f\r\n",pid_l_speed.integral*pid_l_speed.ki);
    //pid_out = ad_speed+pid_out;
    //printf("pid_out = %.1f\r\n",pid_out);
    if(pid_out >= 0) 
    {
        __HAL_TIM_SetCompare(&PWM_TIM, TIM_CHANNEL_1, pid_out);//修改电机PWM占空比
        __HAL_TIM_SetCompare(&PWM_TIM, TIM_CHANNEL_2, 0);//修改电机PWM占空比
    }
    else if(pid_out < 0) 
    {
        __HAL_TIM_SetCompare(&PWM_TIM, TIM_CHANNEL_1, 0);//修改电机PWM占空比
        __HAL_TIM_SetCompare(&PWM_TIM, TIM_CHANNEL_2, pid_out);//修改电机PWM占空比
    }
}

/****************************************
 * 作用：设置右边电机速度
 * 参数：PID参数结构体地址；目标值；反馈值
 * 返回值：无
 * ****************************************/
void Set_Right_Speed(float target,int16_t ad_speed)
{
    float pid_out = 0;
    if(target >= 180) target = 180;
    if(target < -180) target = -180;
	target = target + ad_speed;
    pid_out = Speed_PID_Realize(&pid_r_speed,target,motor_right.speed);
    //pid_out = ad_speed+pid_out;
    if(pid_out >= 0) 
    {
        __HAL_TIM_SetCompare(&PWM_TIM, TIM_CHANNEL_3, pid_out);//修改电机PWM占空比
        __HAL_TIM_SetCompare(&PWM_TIM, TIM_CHANNEL_4, 0);//修改电机PWM占空比
    }
    else if(pid_out < 0) 
    {
        __HAL_TIM_SetCompare(&PWM_TIM, TIM_CHANNEL_3, 0);//修改电机PWM占空比
        __HAL_TIM_SetCompare(&PWM_TIM, TIM_CHANNEL_4, pid_out);//修改电机PWM占空比
    }

}

/****************************************
 * 作用：位置PID设置小车行驶距离
 * 参数：行驶距离，差速
 * 返回值：无
 * ****************************************/
void Set_Left_Location(float distance)
{
    float tar_speed = 0;
    tar_speed = Location_PID_Realize(&pid_l_position,distance,motor_left.totalCount);
    //if(tar_speed > 85) tar_speed = 85;
    //if(tar_speed < -85) tar_speed = -85;
    Set_Left_Speed(tar_speed,0);
}

/****************************************
 * 作用：位置PID设置小车行驶距离
 * 参数：行驶距离，差速
 * 返回值：无
 * ****************************************/
void Set_Right_Location(float distance)
{
    float tar_speed = 0; 
    tar_speed = Location_PID_Realize(&pid_r_position,distance,motor_right.totalCount);    
    //if(tar_speed > 85) tar_speed = 85;		
    //if(tar_speed < -85) tar_speed = -85;
    Set_Right_Speed(tar_speed,0);
}

/****************************************
 * 作用：位置PID设置小车转弯
 * 参数：行驶距离，差速
 * 返回值：无
 * ****************************************/
void Set_Turn_Angle(float angle)
{
    float tar_speed = 0;
    tar_speed = Location_PID_Realize(&pid_l_position,angle,angle_z_all);
    //printf("ta%.1f\r\n",angle);
    if(tar_speed > FOR_SPEED) tar_speed = FOR_SPEED;
    if(tar_speed < -FOR_SPEED) tar_speed = -FOR_SPEED;
    //printf("aa%.1f\r\n",angle_z_all);
    Set_Left_Speed(-tar_speed,0);
    Set_Right_Speed(tar_speed,0);

    
}

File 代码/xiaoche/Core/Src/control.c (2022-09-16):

#include "control.h"
int8_t life_led_count = 0,life_led_state = 1;
extern PID pid_l_speed,pid_l_position,pid_r_speed,pid_r_position;
extern Motor motor_right,motor_left;
int8_t tarspeed_left = 0,tarspeed_right = 0; 

extern uint8_t Rx2Buffer[5];//串口2接收数据存放的变量
extern float angle_z,angle_z_all;
extern uint32_t angle_z_temp;
extern int32_t JY901_Init_val[4];
extern uint8_t run_mode,run_mode_temp;
uint16_t time_count = 0,time_count_flag = 0;
extern int8_t jy901_of_count;
uint8_t speed_flag = 0,angle_flag = 0;
int32_t tar_angle = 0;
extern uint8_t init_count;
uint8_t step_count = 1;
extern int32_t tar_direct;
uint8_t angle_once = 1;
uint8_t time_change = 0;

/***************************************
 * 串口接收中断函数
 * USART1: 115200
 * USART2: 9600
 * USART3: 9600
 * ************************************/
void HAL_UART_RxCpltCallback(UART_HandleTypeDef *huart)
{
    //JY901_UART_RxCpltCallback(huart);//串口3 JY901
    BLUETOOTH_UART_RxCpltCallback(huart);//串口2 蓝牙
}

/***************************************
 * 定时器中断函数
 * 频率：20Hz
 * ************************************/
void HAL_TIM_PeriodElapsedCallback(TIM_HandleTypeDef *htim)
{
    Motor_Get_Speed(htim);//得到电机转速
    if(htim->Instance==GAP_TIM.Instance)
    {
        //Life_Led();//LED生命指示灯
        life_led_count++;
        //printf("%.2f",motor_left.speed);
        //printf(",");
        //printf("%.2f\r\n",motor_right.speed);
        //printf("motor_right.totalCount = %d\r\n",motor_right.totalCount);
        //printf("motor_right.overflowNum = %d\r\n",motor_right.overflowNum);
        
        if(speed_flag == 1)
        {
            Set_Right_Speed(tarspeed_left,-((angle_z_temp - tar_direct)*1));
            Set_Left_Speed(tarspeed_right,(angle_z_temp - tar_direct)*1);
        }
        else if(angle_flag == 1)
        {
            Set_Turn_Angle(tar_angle);
        }
        //printf("al%.1f\r\n",angle_z_all);
        //printf("tr%d,",tar_angle);
        //printf("td%d\r\n",tar_direct);
        //printf("in = %d\r\n",JY901_Init_val[3]);
        //printf("count = %d\r\n",init_count);
        //printf("%.1f\r\n",(float)(angle_z_temp - JY901_Init_val[3]));
        //printf("tar_angle = %d\r\n",tar_angle);
        //printf("%.1f\r\n",angle_z_all);
        //printf("ct%d,",step_count);
        //printf("di%d,",tar_direct);
        //printf("temp%d\r\n",angle_z_temp);
        // for(uint8_t k = 0;k<5;k++)
        // {
        //     printf("%d ",Rx2Buffer[k]);
        // }
        // printf("\r\n");
        //printf("mode%d\r\n",run_mode);
        // if(run_mode != 0)
        // {
        //     printf("st%d\r\n",step_count);
        // }
        
        if(time_count_flag == 1)
            time_count++;
    } 
    
}

/*********************************
 * 功能：板载LED闪烁，生命指示灯
 * 输入：无
 * 返回值：无
 * *******************************/
void Life_Led(void)
{
    if(life_led_count < LIFE_LED_TIME_GAP) life_led_count++;
    else if(life_led_count == LIFE_LED_TIME_GAP)
    {
        life_led_state = -life_led_state;
        life_led_count = 1;
    }
    if(life_led_state == 1)
    {
        HAL_GPIO_WritePin(LIFE_LED_GPIO_PORT,LIFE_LED_GPIO_PIN,GPIO_PIN_RESET);//输出低
    }
    else if(life_led_state == -1)
    {
        HAL_GPIO_WritePin(LIFE_LED_GPIO_PORT,LIFE_LED_GPIO_PIN,GPIO_PIN_SET);//输出低
    }
}

/*********************************
 * 功能：基础部分1、2问运行函数
 * 输入：无
 * 返回值：无
 * 
 * *******************************/
void run_one(uint8_t x_scope,uint8_t y_scope)
{
    
    if(x_scope > 4)x_scope = 4;//防止超出场地
    if(y_scope > 3)y_scope = 3;
    //横着走x_scope格
    if((time_count <= FORWARD_GAP_X*x_scope) && step_count == 1)
    {
        //tar_direct = JY901_Init_val[3];
        speed_flag = 1;angle_flag = 0;
        time_count_flag = 1;
        tarspeed_left = FOR_SPEED;tarspeed_right = FOR_SPEED;
    }
    else if((time_count >FORWARD_GAP_X*x_scope) && step_count == 1)
    {
        time_count_flag = 0;
        time_count = 0;
        tarspeed_left = 0;tarspeed_right = 0;
        if(y_scope != 0)step_count++;
        else if(y_scope == 0)
        {
            step_count = 0;
            run_mode = 0;
            tarspeed_left = 0;tarspeed_right = 0;
            time_count_flag = 0;
            time_count = 0;
        }
    } 

    //右转90°
    if(step_count == 2 && angle_once == 1)
    {
        speed_flag = 0;angle_flag = 1;
        tar_direct = tar_direct - 90;
        tar_angle = angle_z_all - 90;
        angle_once = 0;
    }
    else if(step_count == 2 && angle_once == 0 && abs(tar_angle - angle_z_all) == 0)
    {
        //HAL_Delay(200);
        pid_l_speed.integral = 0;//积分清零
        pid_r_speed.integral = 0;
        step_count++;
        angle_once = 1;

    }

    //竖着着走y_scope格
    if((time_count <= FORWARD_GAP_Y*y_scope) && step_count == 3)
    {
        
        time_count_flag = 1;
        tarspeed_left = FOR_SPEED;tarspeed_right = FOR_SPEED;
        speed_flag = 1;angle_flag = 0;
    }
    else if((time_count >FORWARD_GAP_Y*y_scope) && step_count == 3)
    {
        time_count_flag = 0;
        time_count = 0;
        tarspeed_left = 0;tarspeed_right = 0;
        //speed_flag = 0;angle_flag = 0;
        step_count++;
        step_count = 0;
        run_mode = 0;
        HAL_GPIO_WritePin(LIFE_LED_GPIO_PORT,LIFE_LED_GPIO_PIN,GPIO_PIN_SET);//输出低
    }
    
}
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

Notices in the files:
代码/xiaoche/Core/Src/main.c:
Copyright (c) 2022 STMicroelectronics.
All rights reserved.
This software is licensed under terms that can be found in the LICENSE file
